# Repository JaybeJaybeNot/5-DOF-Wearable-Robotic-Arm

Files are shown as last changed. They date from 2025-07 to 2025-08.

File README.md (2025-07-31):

Robotic arms are a common project idea for engineers, providing the opportunity to tackle challenges such as feedback loops, PCB designing, firmware programming, and mechanical designing. The difficulty varies greatly, from using basic Microservos driven by Arduino to using industry-standard MCUs like the STM32 family to achieve impressive torque, precision, accuracy, and speed. 
Our design will lean somewhat to the right (industry-like) side of difficulty, utilizing the STM32F103C8Tx model of MCU's for performance, TMC motor drivers, the motors will be  2 NEMA 23 (QSH6018) for shoulders, and NEMA 17 (QSH6018) for elbow. Stepper motors are chosen for their high torque relative to their low costs, possibly getting away with $30 for each NEMA 23, depending on the seller. Gearboxes will be utilized for each motor to increase torque output. We'll also lean into the gritty, brutalist aesthetic of industry, partially because I had minimal CAD experience at the beginning of this project.
The "quirk" of our project is that the robotic arm will be wearable. Current design ideas include straps similar to those of a hiking backpack, but will possible change in the future due to ergonomic reasons or if I just came up with better ideas. To control the robotic arm, a GUI will be made with sliders that control each joint, and activators for motor modes (Stealthchop2, spreadcycle). 

This project was made out of a desire to learn embedded systems, firmware code, and basic mechanical design. It is also partially motivated by having Viktor from Arcane as my favorite character. 

Screenshot 2025-07-26 at 5 40 39 AM
Screenshot 2025-07-31 at 12 21 03 AM
Screenshot 2025-07-31 at 12 26 04 AM

|120R1 |FerriteBead |~ |Inductor_SMD:L_0402_1005Metric |1  |FIELD6|
|---|---|---|---|---|---|
|C1 |680 uF |~ |Capacitor_SMD:C_1210_3225Metric |1  | |
|C2 |220 uF |~ |Capacitor_SMD:C_0603_1608Metric |1  | |
|C3,C15 |10 pF |~ |-- mixed values -- |2  | |
|C4,C18,C19,C22,C25,C26,C27,C28|100nF |~ |-- mixed values -- |8  | |
|C5,C24 |2.2u, 6.3v |~ |-- mixed values -- |2  | |
|C6,C7,C8,C9,C14 |100 nF |~ |Capacitor_SMD:C_0201_0603Metric |5  | |
|C10 |10 uF |~ |Capacitor_SMD:C_0201_0603Metric |1  | |
|C11 |10 nF |~ |Capacitor_SMD:C_0201_0603Metric |1  | |
|C12,C13 |1 uF |~ |Capacitor_SMD:C_0201_0603Metric |2  | |
|C16,C17 |22 uF |~ |Capacitor_SMD:C_0201_0603Metric |2  | |
|C20,C29 |100uF |~ |Capacitor_SMD:CP_Elec_5x3.9 |2  | |
|C21,C23 |22nF |~ |Capacitor_SMD:C_0201_0603Metric |2  | |
|D1 |1N5824 |http://www.vishay.com/docs/88526/1n5820.pdf |Diode_THT:D_DO-201AD_P3.81mm_Vertical_AnodeUp |1  | |
|D2 |LED |~ |LED_THT:LED_D2.0mm_W4.0mm_H2.8mm_FlatTop |1  | |
|J1,J2 |Conn_01x04_Pin |~ |Connector:FanPinHeader_1x04_P2.54mm_Vertical |2  | |
|J3,J4,J5,J6,J7,J8,J9,J10 |Screw_Terminal_01x01|~ |TerminalBlock_MetzConnect:TerminalBlock_MetzConnect_360271_1x01_Horizontal_ScrewM3.0_Boxed|8  | |
|J11 |Supply anode |~ |TerminalBlock_Phoenix:TerminalBlock_Phoenix_MKDS-1,5-2-5.08_1x02_P5.08mm_Horizontal |1  | |
|J12 |Supply Cathode |~ |TerminalBlock_Phoenix:TerminalBlock_Phoenix_MKDS-1,5-2-5.08_1x02_P5.08mm_Horizontal |1  | |
|L1 |33 uH |~ |Inductor_SMD:L_0603_1608Metric |1  | |
|P1 |USB_C_Plug_USB2.0 |https://www.usb.org/sites/default/files/documents/usb_type-c.zip|Connector_USB:USB_C_Plug_JAE_DX07P024AJ1 |1  | |
|R1 |10k |~ |Resistor_SMD:R_0603_1608Metric |1  | |
|R2,R11,R12 |5.1kR |~ |Resistor_SMD:R_0603_1608Metric |3  | |
|R3,R4,R5,R6 |1.5k |~ |Resistor_SMD:R_0603_1608Metric |4  | |
|R7,R8,R9,R10 |0.05 R |~ |Resistor_SMD:R_0603_1608Metric |4  | |
|RREF1,RREF2 |0.05R |~ |Resistor_SMD:R_0603_1608Metric |2  | |
|SW1 |SW_DPST_x2 |~ |Button_Switch_SMD:SW_SPST_REED_CT05-XXXX-J1 |1  | |
|SW2 |SW_SPDT |~ |Button_Switch_THT:SW_Slide_SPDT_Straight_CK_OS102011MS2Q |1  | |
|U1 |STM32F103C8Tx |https://www.st.com/resource/en/datasheet/stm32f103c8.pdf |Package_QFP:LQFP-48_7x7mm_P0.5mm |1  | |
|U2 |AMS1117-3.3 |http://www.advanced-monolithic.com/pdf/ds1117.pdf |Package_TO_SOT_SMD:SOT-223-3_TabPin2 |1  | |
|U3,U5 |TMC2209-LA |TMC2209-LA |footprints:QFN28_5X5_TRI |2  | |
|U4 |LM2596S-3.3 |http://www.ti.com/lit/ds/symlink/lm2596.pdf |Package_TO_SOT_SMD:TO-263-5_TabPin3 |1  | |
|Y1 |16 MHz |~ |Crystal:Crystal_SMD_0603-4Pin_6.0x3.5mm |1  | |

|Part Name |FIXED Modular design|FIELD3 |FIELD4 |FIELD5|FIELD6 |FIELD7 |FIELD8 |FIELD9  |FIELD10|FIELD11 |FIELD12 |FIELD13 |
|---|---|---|---|---|---|---|---|---|---|---|---|---|
|Working BOM |as of July 31, 2025 at 12:54:05 AM UTC| | | | | | | | | | | |
|Exported by |yaoy26@okemosk12.net| | | | | | | | | | | |
|Time of Export |12:54 AM Jul 31, 2025| | | | | | | | | | | |
| | | | | | | | | | | | | |
|Level |Part Number |Part Name |External Component |Milestone|Description |Link |Lifecycle|Revision|State  |Quantity|Material Name|Change Order|
|1 |FIXED Modular design|FIXED Modular design | | | | | | |Working|1 |Steel | |
|1.1 |90304A311_Steel Pan Head Torx Screws|90304A311_Steel Pan Head Torx Screws |External | |STEP AP203 | | | |Working|1 |Steel | |
|1.2 |FLANGE_COUPLING_W_GRUB_SCREW_ASM|flange_coupling_w_grub_screw_asm |External | | |[(May not work on some browsers)](https://www.aliexpress.us/item/3256801265414698.html?gatewayAdapt=glo2usa4itemAdapt)| | |Working|1 |Steel | |
|1.2.1 |M6X8_GRUB_SCREW |M6X8_GRUB_SCREW | | |NOT SPECIFIED | | | |Working|1 |Steel | |
|1.2.2 |FLANGE_COUPLING_W_KEYWAY|FLANGE_COUPLING_W_KEYWAY | | |NOT SPECIFIED |https://www.aliexpress.us/item/2255800648228548.html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| | |Working|3 |Steel | |
|1.3 |23HS22-2804S-HG50 |23HS22-2804S-HG50 |External | |STEP AP214 |https://www.omc-stepperonline.com/nema-23-stepper-motor-l-56mm-gear-ratio-50-1-high-precision-planetary-gearbox-23hs22-2804s-hg50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| | |Working|4 |Steel | |
|1.4.1 |M6X8_GRUB_SCREW |M6X8_GRUB_SCREW (2) | | |NOT SPECIFIED | | | |Working|1 |Steel | |
| | | | | | | | | | | | | |
|1.5 |90304A311_Steel Pan Head Torx Screws|90304A311_Steel Pan Head Torx Screws v1 (1) | | |STEP AP203 | | | |Working|1 |Steel | |
|1.6 |Base2 |Base2 | | | | | | |Working|1 |Steel | |
|1.7 |Link 2 |Link 2 | | | | | | |Working|1 |Steel | |
|1.7.1 |ST-M2 |ST-M2 v1 (1) | | |STEP AP214 |https://www.omc-stepperonline.com/nema-23-bracket-for-stepper-motor-and-geared-stepper-motor-alloy-steel-bracket-st-m2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| | |Working|4 |Steel | |
|1.9 |Base1 |Base1 | | | | | | |Working|1 |Steel | |

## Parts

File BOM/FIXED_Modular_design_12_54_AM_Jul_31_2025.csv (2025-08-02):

Part Name | FIXED Modular design
Working BOM | as of July 31, 2025 at 12:54:05 AM UTC
Exported by | yaoy26@okemosk12.net
Time of Export | 12:54 AM Jul 31, 2025
Level | Part Number | Part Name | External Component | Milestone | Description | Item Number | Lifecycle | Revision | State | Quantity | Material Name | Change Order
1 | FIXED Modular design | FIXED Modular design |  |  |  |  |  |  | Working | 1 | Steel
1.1 | 90304A311_Steel Pan Head Torx Screws | 90304A311_Steel Pan Head Torx Screws | External |  | STEP AP203 |  |  |  | Working | 1 | Steel
1.2 | FLANGE_COUPLING_W_GRUB_SCREW_ASM | flange_coupling_w_grub_screw_asm | External |  |  |  |  |  | Working | 1 | Steel
1.2.1 | M6X8_GRUB_SCREW | M6X8_GRUB_SCREW |  |  | NOT SPECIFIED |  |  |  | Working | 1 | Steel
1.2.2 | FLANGE_COUPLING_W_KEYWAY | FLANGE_COUPLING_W_KEYWAY |  |  | NOT SPECIFIED |  |  |  | Working | 1 | Steel
1.3 | 23HS22-2804S-HG50 | 23HS22-2804S-HG50 | External |  | STEP AP214 |  |  |  | Working | 1 | Steel
1.4 | FLANGE_COUPLING_W_GRUB_SCREW_ASM | flange_coupling_w_grub_screw_asm v1 (2) |  |  |  |  |  |  | Working | 1 | Steel
1.4.1 | M6X8_GRUB_SCREW | M6X8_GRUB_SCREW (2) |  |  | NOT SPECIFIED |  |  |  | Working | 1 | Steel
1.4.2 | FLANGE_COUPLING_W_KEYWAY | FLANGE_COUPLING_W_KEYWAY (2) |  |  | NOT SPECIFIED |  |  |  | Working | 1 | Steel
1.5 | 90304A311_Steel Pan Head Torx Screws | 90304A311_Steel Pan Head Torx Screws v1 (1) |  |  | STEP AP203 |  |  |  | Working | 1 | Steel
1.6 | Base2 | Base2 |  |  |  |  |  |  | Working | 1 | Steel
1.7 | Link 2 | Link 2 |  |  |  |  |  |  | Working | 1 | Steel
1.7.1 | ST-M2 | ST-M2 v1 (1) |  |  | STEP AP214 |  |  |  | Working | 1 | Steel
1.8 | 23HS22-2804S-HG50 | 23HS22-2804S-HG50 v1 (2) |  |  | STEP AP214 |  |  |  | Working | 1 | Steel
1.9 | Base1 | Base1 |  |  |  |  |  |  | Working | 1 | Steel
1.10 | 23HS22-2804S-HG50 | 23HS22-2804S-HG50 v1 |  |  | STEP AP214 |  |  |  | Working | 1 | Steel
1.11 | STM32 Other motors 1 | STM32 Other motors v1 |  |  | KiCad electronic assembly |  |  |  | Working | 1 | Steel
1.11.1 | TerminalBlock_Phoenix_MKDS-1,5-2-5.08_1x02_P5.08mm_Horizontal | TerminalBlock_Phoenix_MKDS-1,5-2-5.08_1x02_P5.08mm_Horizontal |  |  |  |  |  |  | Working | 2 | Steel
1.11.1.1 | TerminalBlock_Phoenix_MKDS_15_2_508_1x02_P508mm_Horizontal | TerminalBlock_Phoenix_MKDS_15_2_508_1x02_P508mm_Horizontal |  |  |  |  |  |  | Working | 1 | Steel
1.11.2 | FanPinHeader_1x04_P2.54mm_Vertical | FanPinHeader_1x04_P2.54mm_Vertical |  |  |  |  |  |  | Working | 2 | Steel
1.11.2.1 | Fan_Pin_Header_Straight_1x04 | Fan_Pin_Header_Straight_1x04 |  |  |  |  |  |  | Working | 1 | Steel
1.11.3 | C_0201_0603Metric | C_0201_0603Metric (1) |  |  |  |  |  |  | Working | 4 | Steel
1.11.3.1 | C_0201_0603Metric | C_0201_0603Metric |  |  |  |  |  |  | Working | 1 | Steel
1.11.4 | R_0402_1005Metric | R_0402_1005Metric (1) |  |  |  |  |  |  | Working | 7 | Steel
1.11.4.1 | R_0402_1005Metric | R_0402_1005Metric |  |  |  |  |  |  | Working | 1 | Steel
1.11.5 | C_01005_0402Metric | C_01005_0402Metric (1) |  |  |  |  |  |  | Working | 18 | Steel
1.11.5.1 | C_01005_0402Metric | C_01005_0402Metric |  |  |  |  |  |  | Working | 1 | Steel
1.11.6 | R_0201_0603Metric | R_0201_0603Metric (1) |  |  |  |  |  |  | Working | 2 | Steel
1.11.6.1 | R_0201_0603Metric | R_0201_0603Metric |  |  |  |  |  |  | Working | 1 | Steel
1.11.7 | C_0402_1005Metric | C_0402_1005Metric (1) |  |  |  |  |  |  | Working | 3 | Steel
1.11.7.1 | C_0402_1005Metric | C_0402_1005Metric |  |  |  |  |  |  | Working | 1 | Steel
1.11.8 | CP_Elec_5x3.9 | CP_Elec_5x3.9 |  |  |  |  |  |  | Working | 2 | Steel
1.11.8.1 | CP_Elec_5x39 | CP_Elec_5x39 |  |  |  |  |  |  | Working | 1 | Steel
1.11.9 | C_1210_3225Metric | C_1210_3225Metric (1) |  |  |  |  |  |  | Working | 1 | Steel
1.11.9.1 | C_1210_3225Metric | C_1210_3225Metric |  |  |  |  |  |  | Working | 1 | Steel
1.11.10 | LQFP-48_7x7mm_P0.5mm | LQFP-48_7x7mm_P0.5mm |  |  |  |  |  |  | Working | 1 | Steel
1.11.10.1 | LQFP_48_7x7mm_P05mm | LQFP_48_7x7mm_P05mm |  |  |  |  |  |  | Working | 1 | Steel
1.11.11 | R_1206_3216Metric | R_1206_3216Metric (1) |  |  |  |  |  |  | Working | 4 | Steel
1.11.11.1 | R_1206_3216Metric | R_1206_3216Metric |  |  |  |  |  |  | Working | 1 | Steel
1.11.12 | TO-263-5_TabPin3 | TO-263-5_TabPin3 |  |  |  |  |  |  | Working | 1 | Steel
1.11.12.1 | CQ assembly | CQ assembly |  |  |  |  |  |  | Working | 1 | Steel
1.11.13 | R_0805_2012Metric | R_0805_2012Metric (1) |  |  |  |  |  |  | Working | 1 | Steel
1.11.13.1 | R_0805_2012Metric | R_0805_2012Metric |  |  |  |  |  |  | Working | 1 | Steel
1.11.14 | STM32 Other motors_PCB | STM32 Other motors_PCB |  |  |  |  |  |  | Working | 1 | Steel
1.11.15 | C_0603_1608Metric | C_0603_1608Metric (1) |  |  |  |  |  |  | Working | 1 | Steel
1.11.15.1 | C_0603_1608Metric | C_0603_1608Metric |  |  |  |  |  |  | Working | 1 | Steel
1.11.16 | SW_Slide_SPDT_Straight_CK_OS102011MS2Q | SW_Slide_SPDT_Straight_CK_OS102011MS2Q (1) |  |  |  |  |  |  | Working | 1 | Steel
1.11.16.1 | SW_Slide_SPDT_Straight_CK_OS102011MS2Q | SW_Slide_SPDT_Straight_CK_OS102011MS2Q |  |  |  |  |  |  | Working | 1 | Steel
1.11.17 | SW_SPST_REED_CT05-XXXX-J1 | SW_SPST_REED_CT05-XXXX-J1 |  |  |  |  |  |  | Working | 1 | Steel
1.11.17.1 | ASSEMBLY | ASSEMBLY |  |  |  |  |  |  | Working | 1 | Steel
1.11.18 | LED_D2.0mm_W4.0mm_H2.8mm_FlatTop | LED_D2.0mm_W4.0mm_H2.8mm_FlatTop (1) |  |  |  |  |  |  | Working | 1 | Steel
1.11.18.1 | LED_D2.0mm_W4.0mm_H2.8mm_FlatTop | LED_D2.0mm_W4.0mm_H2.8mm_FlatTop |  |  |  |  |  |  | Working | 1 | Steel
1.11.19 | L_0402_1005Metric | L_0402_1005Metric (1) |  |  |  |  |  |  | Working | 2 | Steel
1.11.19.1 | L_0402_1005Metric | L_0402_1005Metric |  |  |  |  |  |  | Working | 1 | Steel
1.11.20 | SOT-223 | SOT-223 |  |  |  |  |  |  | Working | 1 | Steel
1.11.20.1 | SOT_223 | SOT_223 |  |  |  |  |  |  | Working | 1 | Steel
1.11.21 | Crystal_SMD_0603-4Pin_6.0x3.5mm | Crystal_SMD_0603-4Pin_6.0x3.5mm |  |  |  |  |  |  | Working | 1 | Steel
1.11.21.1 | SMD_0603_4Pin | SMD_0603_4Pin |  |  |  |  |  |  | Working | 1 | Steel
1.12 | ST-M2 | ST-M2 v1 |  |  | STEP AP214 |  |  |  | Working | 1 | Steel
1.13 | FLANGE_COUPLING_W_GRUB_SCREW_ASM | flange_coupling_w_grub_screw_asm v1 |  |  |  |  |  |  | Working | 1 | Steel
1.13.1 | FLANGE_COUPLING_W_KEYWAY | FLANGE_COUPLING_W_KEYWAY |  |  | NOT SPECIFIED |  |  |  | Working | 1 | Steel
1.13.2 | M6X8_GRUB_SCREW | M6X8_GRUB_SCREW |  |  | NOT SPECIFIED |  |  |  | Working | 1 | Steel
1.14 | Base2 (1) | Base2 (1) |  |  |  |  |  |  | Working | 1 | Steel
1.15 | STM32 Other motors 1 | STM32 Other motors v1 (1) |  |  | KiCad electronic assembly |  |  |  | Working | 1 | Steel
1.15.1 | C_01005_0402Metric | C_01005_0402Metric (1) (1) |  |  |  |  |  |  | Working | 18 | Steel
1.15.1.1 | C_01005_0402Metric | C_01005_0402Metric (2) |  |  |  |  |  |  | Working | 1 | Steel
1.15.2 | SOT-223 | SOT-223 (1) |  |  |  |  |  |  | Working | 1 | Steel
1.15.2.1 | SOT_223 | SOT_223 (1) |  |  |  |  |  |  | Working | 1 | Steel
1.15.3 | R_1206_3216Metric | R_1206_3216Metric (1) (1) |  |  |  |  |  |  | Working | 4 | Steel
1.15.3.1 | R_1206_3216Metric | R_1206_3216Metric (2) |  |  |  |  |  |  | Working | 1 | Steel
1.15.4 | CP_Elec_5x3.9 | CP_Elec_5x3.9 (1) |  |  |  |  |  |  | Working | 2 | Steel
1.15.4.1 | CP_Elec_5x39 | CP_Elec_5x39 (1) |  |  |  |  |  |  | Working | 1 | Steel
1.15.5 | Crystal_SMD_0603-4Pin_6.0x3.5mm | Crystal_SMD_0603-4Pin_6.0x3.5mm (1) |  |  |  |  |  |  | Working | 1 | Steel
1.15.5.1 | SMD_0603_4Pin | SMD_0603_4Pin (1) |  |  |  |  |  |  | Working | 1 | Steel
1.15.6 | C_0201_0603Metric | C_0201_0603Metric (1) (1) |  |  |  |  |  |  | Working | 4 | Steel
1.15.6.1 | C_0201_0603Metric | C_0201_0603Metric (2) |  |  |  |  |  |  | Working | 1 | Steel
1.15.7 | R_0402_1005Metric | R_0402_1005Metric (1) (1) |  |  |  |  |  |  | Working | 7 | Steel
1.15.7.1 | R_0402_1005Metric | R_0402_1005Metric (2) |  |  |  |  |  |  | Working | 1 | Steel
1.15.8 | TerminalBlock_Phoenix_MKDS-1,5-2-5.08_1x02_P5.08mm_Horizontal | TerminalBlock_Phoenix_MKDS-1,5-2-5.08_1x02_P5.08mm_Horizontal (1) |  |  |  |  |  |  | Working | 2 | Steel
1.15.8.1 | TerminalBlock_Phoenix_MKDS_15_2_508_1x02_P508mm_Horizontal | TerminalBlock_Phoenix_MKDS_15_2_508_1x02_P508mm_Horizontal (1) |  |  |  |  |  |  | Working | 1 | Steel
1.15.9 | LED_D2.0mm_W4.0mm_H2.8mm_FlatTop | LED_D2.0mm_W4.0mm_H2.8mm_FlatTop (1) (1) |  |  |  |  |  |  | Working | 1 | Steel
1.15.9.1 | LED_D2.0mm_W4.0mm_H2.8mm_FlatTop | LED_D2.0mm_W4.0mm_H2.8mm_FlatTop (2) |  |  |  |  |  |  | Working | 1 | Steel
1.15.10 | TO-263-5_TabPin3 | TO-263-5_TabPin3 (1) |  |  |  |  |  |  | Working | 1 | Steel
1.15.10.1 | CQ assembly | CQ assembly (1) |  |  |  |  |  |  | Working | 1 | Steel
1.15.11 | R_0201_0603Metric | R_0201_0603Metric (1) (1) |  |  |  |  |  |  | Working | 2 | Steel
1.15.11.1 | R_0201_0603Metric | R_0201_0603Metric (2) |  |  |  |  |  |  | Working | 1 | Steel
1.15.12 | C_0402_1005Metric | C_0402_1005Metric (1) (1) |  |  |  |  |  |  | Working | 3 | Steel
1.15.12.1 | C_0402_1005Metric | C_0402_1005Metric (2) |  |  |  |  |  |  | Working | 1 | Steel
1.15.13 | FanPinHeader_1x04_P2.54mm_Vertical | FanPinHeader_1x04_P2.54mm_Vertical (1) |  |  |  |  |  |  | Working | 2 | Steel
1.15.13.1 | Fan_Pin_Header_Straight_1x04 | Fan_Pin_Header_Straight_1x04 (1) |  |  |  |  |  |  | Working | 1 | Steel
1.15.14 | R_0805_2012Metric | R_0805_2012Metric (1) (1) |  |  |  |  |  |  | Working | 1 | Steel
1.15.14.1 | R_0805_2012Metric | R_0805_2012Metric (2) |  |  |  |  |  |  | Working | 1 | Steel
1.15.15 | LQFP-48_7x7mm_P0.5mm | LQFP-48_7x7mm_P0.5mm (1) |  |  |  |  |  |  | Working | 1 | Steel
1.15.15.1 | LQFP_48_7x7mm_P05mm | LQFP_48_7x7mm_P05mm (1) |  |  |  |  |  |  | Working | 1 | Steel
1.15.16 | SW_Slide_SPDT_Straight_CK_OS102011MS2Q | SW_Slide_SPDT_Straight_CK_OS102011MS2Q (1) (1) |  |  |  |  |  |  | Working | 1 | Steel
1.15.16.1 | SW_Slide_SPDT_Straight_CK_OS102011MS2Q | SW_Slide_SPDT_Straight_CK_OS102011MS2Q (2) |  |  |  |  |  |  | Working | 1 | Steel
1.15.17 | L_0402_1005Metric | L_0402_1005Metric (1) (1) |  |  |  |  |  |  | Working | 2 | Steel
1.15.17.1 | L_0402_1005Metric | L_0402_1005Metric (2) |  |  |  |  |  |  | Working | 1 | Steel
1.15.18 | STM32 Other motors_PCB | STM32 Other motors_PCB (1) |  |  |  |  |  |  | Working | 1 | Steel
1.15.19 | C_1210_3225Metric | C_1210_3225Metric (1) (1) |  |  |  |  |  |  | Working | 1 | Steel
1.15.19.1 | C_1210_3225Metric | C_1210_3225Metric (2) |  |  |  |  |  |  | Working | 1 | Steel
1.15.20 | SW_SPST_REED_CT05-XXXX-J1 | SW_SPST_REED_CT05-XXXX-J1 (1) |  |  |  |  |  |  | Working | 1 | Steel
1.15.20.1 | ASSEMBLY | ASSEMBLY (1) |  |  |  |  |  |  | Working | 1 | Steel
1.15.21 | C_0603_1608Metric | C_0603_1608Metric (1) (1) |  |  |  |  |  |  | Working | 1 | Steel
1.15.21.1 | C_0603_1608Metric | C_0603_1608Metric (2) |  |  |  |  |  |  | Working | 1 | Steel
1.16 | ST-M2 | ST-M2 v1 (2) |  |  | STEP AP214 |  |  |  | Working | 1 | Steel
1.17 | bananaforscale | bananaforscale v1 |  |  |  |  |  |  | Working | 1 | Steel
1.18 | 23HS22-2804S-HG50 | 23HS22-2804S-HG50 v1 (1) |  |  | STEP AP214 |  |  |  | Working | 1 | Steel
1.19 | Link1 | Link1 |  |  |  |  |  |  | Working | 1 | Steel
1.20 | FLANGE_COUPLING_W_GRUB_SCREW_ASM | flange_coupling_w_grub_screw_asm v1 (1) |  |  |  |  |  |  | Working | 1 | Steel
1.20.1 | FLANGE_COUPLING_W_KEYWAY | FLANGE_COUPLING_W_KEYWAY (1) |  |  | NOT SPECIFIED |  |  |  | Working | 1 | Steel
1.20.2 | M6X8_GRUB_SCREW | M6X8_GRUB_SCREW (1) |  |  | NOT SPECIFIED |  |  |  | Working | 1 | Steel
1.21 | 90304A311_Steel Pan Head Torx Screws | 90304A311_Steel Pan Head Torx Screws v1 |  |  | STEP AP203 |  |  |  | Working | 1 | Steel

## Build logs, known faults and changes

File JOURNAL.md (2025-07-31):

---
Title: "Wearable 5 axis Robotic Arm"
author: "Yugang Yao"
description: "Fully custom stepper motor robotic arm you can wear on your back, operating like a fully controllable third arm by interacting with a GUI."
created at: 2025-7-4
TOTAL HOURS: 50 Hr 15 Minutes (Not including time spent planning, debugging, or reading datasheets because I didn't record them)
---

$${\color{white}06/15/2025 \space project \space statement \space and \space planning}$$

I have an idea!

Problem statement: Two arms can get everything done. But a third one can be nifty, huh? Even if it’s for simple applications, it can still be vastly useful. What if you’re holding everything in your two arms, and you need to open a door? What if you are typing and want to get a glass of water to your lips without breaking momentum? What if, possibly, you are performing a surgery and need some assistance? What if you’re doing some sort of combat sport, and want to get a bit creative? What if you just wanna show off at parties?

Objectives: wearable Robotic arm that follows the following specifications:  

5 degrees of freedom: wrist, elbow, shoulder roll, shoulder pitch, gripper. 

Graphical User interface that controls arm movements.

minimum payload 100-300 g

Angular accuracy: +/- 2-3 degrees with high-resolution servos or steppers+encoders

Position repeatability: 1-2 mm at full reach. Depends on backlash and compliance

Backlash: <0.5mm. Use zero backlash gearboxes or direct drive.

Delay must be <=500 ms from user input to motor response.

 Should stay relatively still when “attached” to the user’s back
 
Should have a safety mechanism so the user doesn’t get shocked by the 24v battery

I may use the local college’s lab to get some cheap hardware. I doubt they have the exact parts, but they may potentially have potentiometers, resistors, capacitors, Microcontrollers, etc. 

PLANNING:

VNH5019 modules for motor driving have already been designed and are available for $15-20 a pop. You see, we’re kinda budget-tight, so we’re going to design a PCB with 4 of the bare VNH5019A-E ICs–$5 each– to attach to our Maxon EC-i 40 + GP 10 A gearbox. Also note that the VNH5019 only drives brushed motors.

$${\color{white}5/16/2025}$$

Stepper motor possibility (but a few hours later)

The brushed DC motor mentioned earlier is gonna set us back 120 dollars each. We can use a NEMA 23 stepper motor with a large gearbox ratio for the desired torque output instead. Currently thinking 20:1, but I’ll have to see a more experienced engineer later to see if that is possible. Because stepper motors kinda can’t be run using the VNH5019, we’ll instead look into the possibilities of the TMC2226 motor driver. 

Update: We’re going with the NEMA 23 stepper motor with TMC 2226 motor driver

Possibilities of using in revision:
1. harmonic/planatery reducer for motors to extract highest torque instead
2. Using encoders (AS5600, AS5048A) instead of potentiometer for position feedback. Can be a bit more expensive, and we’ll have to learn some things. 

$${\color{white}6/18/2025}$$

Break: Heart project
All that planning for the Robotic arm project is stressing me out. So we’re gonna take a break and make a PCB with LED lights in the shape of a heart, lighting up in sequence. This is the schematics I made. 
Utilizes 2 IC’s:  555 timer to send clock signals in astable mode, and DC4017 to “chase” LEDs in a sequence. Powered by 3 coin batteries, of course. 
Screenshot 2025-07-01 at 11 36 05 AM

I’ll either add this to the robotic arm, or give it as a trinket to my friend. They gave me a heart keychain a few months ago. Regardless, I’ll make the PCB layout for this in my next break. 

I can also possibly modify the design to make it act as an error tester later on the road. 

**1 hour**

$${\color{white}6/22/2026}$$

We’re on vacation, so progress is slow. A wrist-mounted control panel for the arm would be cool as hell, no? We’ll probably have to take on even more disciplines though… Like Embedded UI, power management, and probably ergonomics. Bluetooth for communication, maybe a charge controller for safety, a TFT LCD for affordability and durability, and a MCU for the spi communication; Perhaps an ESP 32 would suit the application. I’ll add this as an idea for next iterations of the arm.

The design for the PCB with the TMC2226-SA motor driver has been commenced, and will probably finish by the end of the day. Moving on next, we’ll figure out the programming and software, and where we can get the mechanical design for the arm. We’ll also tinker around with ROS2, and use Gazebo for simulation (let’s also copy paste the URDF files for the actual arm). My old computer has Ubuntu installed, so let’s do that. 

We can potentially use the 24V battery volt source to power the Nano by using a LM2596 voltage regulator.

Today’s progress (Elbow joint driver and MCU):
Screenshot 2025-06-27 at 9 21 26 PM

**3 hours**

$${\color{white}7/1/2025}$$

Just came back after climbing Mount HuangShan, it was peak (ahahaha).

Anyways, gonna crank out the basic PID code for the arduino nano and for driving the NEMA 17. Honestly, I am quite inexperienced on implementing PID, even though I know alot about the theory. 

I work in bursts anyways, so hopefully I can get most of it done today.
Today’s code:

Screenshot 2025-07-04 at 8 53 39 AM
**3.5 hours**

$${\color{white}7/2/2025}$$

Further project planning + parts selecting

Ok, so, we’re gonna keep the pcb Designs, but there will no longer be any centralized PCB (like as if it’s a critical hit area in a video game). Essentially, the drivers will be placed right next to the motors in the form of small PCB’s, with terminals connecting from the base, which houses the MCU, voltage regulator, and whatnot. Wait, so the 24v power supply to the motors will have a long wire too? I wonder if that’ll introduce even more problems.

To offset this, we’ll make the power supply slightly larger than 24V to compensate for the higher resistance (26v, 28v). We’ll also add a bulk cap (100-470 uF) decoupling capacitor as well as a ceramic cap (0.1-1uF).  right next to Vin of Drivers, as well as ferret beads on the power supply line right before the driver. This is a pretty crude, unelegant method but it’ll probably be enough.

Main reason we’re still using our own design for the motor drivers is because they’re lowk expensive ($30+) and too big to fit in the joints.

Final decision:

Main PCB will sit at base of robotic arm, containing the STM32 Bluepill (STM32F103C8Tx); 2 motor drivers for shoulder yaw and shoulder pitch; and a voltage regulator connected to 24v power source. Elbow joint will have their own motor driver for the TMC2209 NEMA 17

Tmc 2209-LA info:
Footprints and symbol
Datasheet
Finally decided on the specific models:
Nema 17
Nema23
(There are links to these in the original doc)

Reminder, Driver compatibility is about matching current, voltage, and inductance to the driver’s chopping frequency and thermal rating!
Thus, the TCM2226-SA will be used to drive the NEMA 17, while the dual TCM2209-LA will be used to drive the NEMA 23. 
Today's schematic progress (so far):
Screenshot 2025-07-04 at 8 57 01 AM

Iteration for Mark II:
Just watched 稚晖君’s video on his dummy robotic arm, and felt kinda envious when compared to my own design. Thus, I have a wishlist for Mark II in case I build a second robotic arm:
CAN bus
Per-joint MCUs
Force sensors
(Encoders instead of potentiometers)
Sleeker driver IC layouts
Smarter GUI
Power optimization
AI vision 
(optional) glove to control robotic arm movement

For now, we just need to worry about making A robotic arm. 

Taking notes on TMC2209 driver features:

Stealthchop: Silent operation, good for lower velocities

Significantly improved microstepping with low-cost motors - Motor runs smooth and quiet - Absolutely no standby noise - Reduced mechanical resonance yields improved torque

Spreadcycle: Good for higher velocities.

After a few hours, I have finished the schematic FULLY, and have reviewed it to have no errors (so far, I will review it once more when I prepare for PCB layout). Here is the full schematic:Screenshot 2025-07-04 at 2 53 10 PM

I should probably add redundancies for overheating, since running all these on the same PCB will fry it easily. But I feel like moving on to software for now, so that’ll have to wait until I prepare for the PCB layout.

Btw ignore PB5. I've already removed that label; it's just a small error.

**8 hours total**

$${\color{white}7/6/2025}$$

Ok, platformIO is acting up.
Not only did I lose the Main.cpp file for the main PCB board, but I literally can’t find the folder itself. The folder is also nowhere to be seen on the project tab of VScode. 

So, we’re gonna ditch platformIO for STM32CubeIDE.

Hip hip hooray! We get to rewrite the ENTIRE code for the main PCB, but this time in HAL =D! I can’t WAIT to basically learn a whole different language =DDDDDDDD. 

Just played around with STM32cubeIDE for a while, and learned from guides/documentations on youtube. Phil’s Lab my GOAT fr

Screenshot 2025-07-06 at 4 02 45 AM

Ran into some problems with the clock configurations, seems like the APB1 peripheral clock frequency is too low. 

Screenshot 2025-07-06 at 4 02 58 AM

After some tweaking and painfully reading the STM32F1 reference manual, this minor speedbump has been remedied. 

Screenshot 2025-07-06 at 4 03 08 AM

Pins are configured, and so are the clocks. Now all we have to do is figure out how to set the STM32 up to receive serial from the Mac, what to do with certain info, and create the GUI. Finally, we’ll create the 3D physical model and we’ll be done. 

**3 hours**

Note: Kinda been dodging a core problem right now, but we gotta confront the fact that carrying around a 24v battery can kinda cause some lowkey agonizing pain if something goes wrong. So we'll have to overload on safety mechanisms when we get to mechanical design. We'll also have to make additions on our PCB to further prevent overheating

$${\color{white}7/17/2025}$$

Just came back from camp, back to the grind. This also means we’ll have to ramp up productivity. A review of the arm:
Shoulder 
1. will have 3 D.O.F.
2. 2 NEMA motors will be driven by main PCB,
3. 3rd one will be driven by Arduino Nano interfaced via I2C 
STM32F1 will be master MCU. We have 48 MHz of processing power and we will use the full 48 MHz of it!
4.Power source: 24 volts, will be placed in a heavily insulated box to prevent shocks
Elbow:
A singular Arduino nano and TMC driver for Nema 17. 
Further iterations might utilize belts to lower torque on elbow
Wrist: Simple MG90 servo. Just use PWM vro 
GUI: will be built in tkinter. Interfaces with the Uart serial to STM32. 
Alright, today we’ll get serial done, and begin on the mechanical design.

This means we'll gonna have to LEARN UART programming, including HAL and serial parsing. Here's the code so far: Screenshot 2025-07-18 at 9 26 53 PM

**5 Hours**

$${\color{white}7/23/2025-7/25/2025}$$

I have chipped down the DRC more and more on clearance violations, and have connected the pins together finally. We have decided to use GND and power planes for noise and emi reduction, though it will be a bit more expensive. 

We have also finally added PCBway constraints into the settings. Thus, we’ll have to switch from 0402 components to larger ones, because lowk they’re unable to tolerate the close proximity of the components. 

Screenshot 2025-07-26 at 5 03 54 AM

Screenshot 2025-07-26 at 5 04 09 AM

We WILL add heat pours in the future—after finishing the DRC.

I have also met with a longtime friend, a Umich alumni in robotics about this design. he says it’s good so far, so that’s something to think about =].

**12 hours**

May seem like a long time, but trust me, I haven’t done something this complex before so I MUST make sure everything runs as good as possible. 

$${\color{white}7/26/2025}$$

Yayyyy, mechanical design! Woohoo, Yippee.

Constraints:

1. 0.5-1 meters

2. 2 kg payload minimum.

3. Fully covering circuitry

4. Openable via screws to access circuitry and wires

5. Separate compartment for wires and circuitry

6. Hexagonal comb design. Will have one side honeycomb, the other three sides will be solid

7. 25:1 gearboxes, compromise for torque and speed

8. 7075 or 6061 aluminum for linkages. More Carbon fiber towards end of arm. Steel for joints and base.

9. Planetary gearboxes for zero backlash if we can afford it (probably not for the first design. May be employed for future iterations )

10. Modular end factor for different attachable functions. Module will have plugs that attach to end factor to communicate to a microcontroller on what to do. Will also have latches to maintain connection.

Alright, let's get started.

The specs are as follows: shoulder (base) will have 3 degrees of freedom to mimic actual human arm. Will contain the main PCB, alongside slave MCU PCB to drive the additional motor. The motors will all be NEMA 23s.

The elbow joint will be 1 D.O.F. and uses arduino nano + TMC2226SA for the Nema 17. Will also interface with main PCB. Only comment lightly on the fact that we're using I2C protocol for the ~.33m distance between the main mcu and slave mcu.

The wrist will use SG90S microservo. Optional, actually.

Link length from** shoulder joints to elbow joint will be .33 m**. From** elbow to wrist is .46 m.**

All 3 shoulder motors will be placed closely together at the base to reduce torque

**Joints decisions:**

1. Shoulders:

1. Options:

1. Welded Pivot Bracket joint.

1. Pros:

1. extremely strong and rigid,

2. zero backlash.

2. Cons:

3. Permanent. Make a mistake? Womp womp, you can’t fix it.  You also can’t take them out, so they’re not modular

4. You kinda need to know how to weld, and get welding equipment (DEALBREAKER)

2. **Bolt on bracket system (WE’RE USING THIS ONE)**

3. Pros:

5. Still pretty strong

6. Bolted, not welded (NOT DEALBREAKER)

7. Looks pretty clean

2. Elbow:

2. Clevis + Pin Joint.

3. Pro:

4. Can be laser cutted

5. Pretty compact

6. Strong enough

7. VEX robotics people use it

4. Con:

8. Need retainer clips or shoulder bolts

9. **Needs TIGHT tolerances**

Let’s not talk about end effector for now.

Of course, we’ll also need:

1. Bearings

1. 10 mm bore, 26mm OD Flanged bearing

2. Shaft link hub / coupler

3. Shaft collar

4. Mounting brackets or housing to hold bearings in place and constrain all movements except rotation

2. One side must hold rigidity, (bearing pocket or press-fit)

5. Spacer(s) and Shoulder Bolt / Axle Bolt

3. Prevents axial shrifting, keeps rotations smooth

4. Space prevents the bearing from rubbing against joint arm or frame. Shoulder bolt has a section that fits bearing ID perfectly.

We’ll mount the Nema 17 at elbow. But if we NEED to optimize torque, then we can just place them at the back with a belt loop.

rectangular holes are probably for ventilation and weight \; we’ll employ that.

**1 Hour**

**7/27/2025**

Mechanical design marathon.

Aluminum 6061 is very expensive, [datasheet](https://asm.matweb.com/search/specificmaterial.asp?bassnum=ma6061t6) . So here’s the plan:

1. At the base, we’ll use some sort of steel alloy. Cheaper, but 3 times the density

2. Aluminum 5052 could be a substitute.

I feel the plan right now is model a rough diagram of the arm on paper, create a multidimensional function of stress, strain, load, and torque in terms of density of the material selected, and the width/girth of the arm. THEN we'll choose the components based on our application.

Alright, we’ve finished the analysis of the arm at it’s worst scenario: Perfectly horizontal.

Screenshot 2025-07-30 at 5 43 59 PM

**30 minutes**

Not gonna do other angles, because we’ve already accounted for worst case scenario. Also, it’s probably not likely that it’ll just collapse on itself if i raise it perfectly vertical even if the axial stress is at its strongest.

Time for parts selection!

Code for calculations:

import math

==== Inputs ====
Geometry (in meters)
L1 = 0.33      # Length of Link 1

L2 = 0.46      # Length of Link 2

w = 0.1     # Width of rectangular cross-section

h = 0.1       # Height (thickness) of rectangular cross-section

Material (Aluminum 6061-T6)
E = 68.9e9             # Modulus of Elasticity (Pa)

sigma_y = 276e6        # Yield Strength (Pa)

tau_y = 207e6          # Shear Strength (Pa)

fatigue_strength = 96.5e6 # Fatigue Strength (Pa)

Density = 2700 #kg/m^3

Masses (kg)
m1 = L1 * Density * w * h       # Mass of Link 1

m2 = L2 * Density * w * h       # Mass of Link 2

payload = 4200                 # force from punch or weight (Newtons)

Angle of payload force relative to the link axis (in degrees)
theta_deg = 0

theta = math.radians(theta_deg)

Safety Factor
FoS = 1.5

Gravity
g = 9.81  # m/s^2

==== Derived geometric properties ====
A = w * h                         # Cross-sectional area

I = (w * h**3) / 12               # Second moment of area

c = h / 2                         # Distance from neutral axis

==== Forces ====
P_parallel = payload * math.cos(theta) # Axial component

P_perp = payload * math.sin(theta)     # Transverse (bending) component

==== Torques ====
tau_elbow = m2 * g * (L2 / 2) + P_perp * L2

tau_shoulder = (m1 * g * (L1 / 2) +m2 * g * (L1 + L2 / 2) +P_perp * (L1 + L2))

==== Stresses ====
sigma_axial = P_parallel / A

sigma_bending = ((P_perp * (L1 + L2) + (m1 * g * L1/2) + (m2*g*(L1 + L2/2)))  * c) / I

sigma_total = sigma_axial + sigma_bending

AFoS = 276e6 / sigma_total

==== Strain ====
strain = sigma_total / E

==== Deflection ====
Tip deflection of link 2 under end load only
delta = (P_perp * L2**3) / (3 * E * I)

==== Checks ====
print("=== ROBOTIC ARM STRESS REPORT ===")

print(f"Axial Stress:      {sigma_axial/1e6:.2f} MPa")

print(f"Bending Stress:    {sigma_bending/1e6:.2f} MPa")

print(f"Total Stress:      {sigma_total/1e6:.2f} MPa")

print(f"Strain:            {strain:.5e}")

print(f"Deflection (L2):   {delta*1000:.2f} mm")

print(f"Elbow Torque:      {tau_elbow:.2f} Nm")

print(f"Shoulder Torque:   {tau_shoulder:.2f} Nm")

print(f"factor of safety:   {AFoS}")

print("\n=== SAFETY CHECK ===")

print(f"Yield Limit ({sigma_y/FoS/1e6:.2f} MPa) : {'Yessir!' if sigma_total < sigma_y / FoS else 'No =['}")

print(f"Fatigue Limit ({fatigue_strength/FoS/1e6:.2f} MPa): {'Yessir!' if sigma_total < fatigue_strength / FoS else 'No =['}")

print(f"Deflection Check (< {L2/250:.2e} m): {'Yessir!' if delta < L2/250 else 'No =['}")

We’ll play around with the variables until we find something desirable.

****15 minutes****

Ok so, it turns out that if we were to go with a 0.1 m x 0.1 m approximate cross sectional area of the arm using aluminum 6061, we’ll need 28 Nm of torque… Nema 17 can only produce 0.14-0.75 nm max. We’ll have to redo the PCB to change the Nema 17 to a Nema 23. On top of that, aluminum 6061 is frick-ton expensive even if hollow(~$200 for one link), so we’ll have to find other materials and compromise.

Material alternatives:

1. [Steel 1018](https://www.mwcomponents.com/uploads/Resource-Center/Elgin-Material-Sheets/Carbon-Steel-Grade-1018-Data-Sheet_Elgin.pdf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)

1. 370 MPa yield

2. [A36 steel](https://www.ryerson.com/metal-resources/metal-market-intelligence/a36-steel-plate)

2. 248.2 MPa yield

Material selection later. Let’s just design the arm now.

We’ll begin with the joint, constraint definitions: \
1. Houses Nema 23 motor

2. Houses the gearbox along the Nema 23 motor

3. Rotate well

4. Holes for wires to connect with motor

There will be 2 type of joints; the shoulder joint, and elbow joint.

That’s basically it honestly

We originally considered HTD5 timing pulleys, but that’s too mechanically advanced for me. So we’re going to use **NEMA23 ****<span style="text - decoration: underline;">worm**</span>** gearbox (50:1)** as simple add ons to the motor. Cheaper than planetory, and we don’t need industrial level precision so we may get away with $150 total. 

[Nema 23 sizes](http://www.piclist.com/techref/io/stepper/nemasizes.htm)

*Just learned the method is called a **Euler angle joint** chain mimicking the **glenohumeral (shoulder) joint**

The first base will be larger than the second base to compensate for having to carry extra weight. We might have to “overengineer: the coupling between the bases to prevent backlash and slippage. Of course the final rotational joint will just be bolt on bracket.

Enter image alt description
[example image](https://www.researchgate.net/figure/The-iCub-arm-A-CAD-view-of-the-arm-of-the-iCub-robot-with-superimposed-joint-labels-th_fig3_229010855)

Enter image alt description
[inexpensive planetory gearboxes](https://www.omc-stepperonline.com/nema-23-stepper-motor-l-56mm-gear-ratio-50-1-high-precision-planetary-gearbox-23hs22-2804s-hg50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) 

<span style="text - decoration: underline;">**7/29/2025**</span>

(TORQUE POTENTIALLY TOO LOW)

Ugh, it seems we’ll have to go searching for gearboxes again.

We’ll use **Aliexpress** if we need to. 

Screenshot 2025-07-30 at 5 45 40 PM

We’ll add bearings to this sliding point later to both reduce stress on the main motor and to reduce friction. Oh, and the lid for this part will be honeycomb pattern for aesthetics and saving on material.

I’m back with the design, and I just realized.

LOOK AT THE SIZE OF THAT THING HOLY C- BANANA FOR SCALE BY THE WAY.

Screenshot 2025-07-30 at 5 45 59 PM

Realistically, we have 2 options:

1. Redesign the shoulder from scratch

2. Severely cut down on the container size for each motors.

If we go with number 2, which is the most alluring option by far, we might just have the motors exposed. Cuts back on cost and torque too, I guess.

Main issue comes from the motor + gearbox, which is 0.15 m by itself. Holy-

[Direct motor mount](https://www.omc-stepperonline.com/nema-23-bracket-for-stepper-motor-and-geared-stepper-motor-alloy-steel-bracket-st-m2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), we’ll be using this 

Screenshot 2025-07-30 at 5 46 28 PM

Alright, much more manageable now. (Banana for scale)

**5 hours**

7/29/2025

Continued with the mechanical design. We had to dig through various sources to get semi fluent. In short, we’ve decided to use **bracket mounts** to hold the motors in place and **flanged couplers** to get it attached to stuff, ball bearings and honeycomb pattern pending. Of course, there are holes for the I2C wires to go through. 

Finally, we’re finished.

Screenshot 2025-07-30 at 5 46 51 PM

Now all we have to do is provide the wiring diagram, and BOM.
Screenshot 2025-07-30 at 4 51 13 PM
Screenshot 2025-07-30 at 4 46 00 PM
Screenshot 2025-07-30 at 4 37 42 PM
Screenshot 2025-07-30 at 4 36 12 PM
Screenshot 2025-07-30 at 4 31 14 PM

This is the wiring for now. Of course, **We will add clips during assembly to hold the wires down. **

*****8 hours***** (I didn’t know much about mechanical design)

Even if there are many flaws in the design; Ngl, this has been a wild month, and a wild ride. I’ll never forget the 15 hour PCB marathon on the plane. Oh, and I hope my journals entertained somebody.

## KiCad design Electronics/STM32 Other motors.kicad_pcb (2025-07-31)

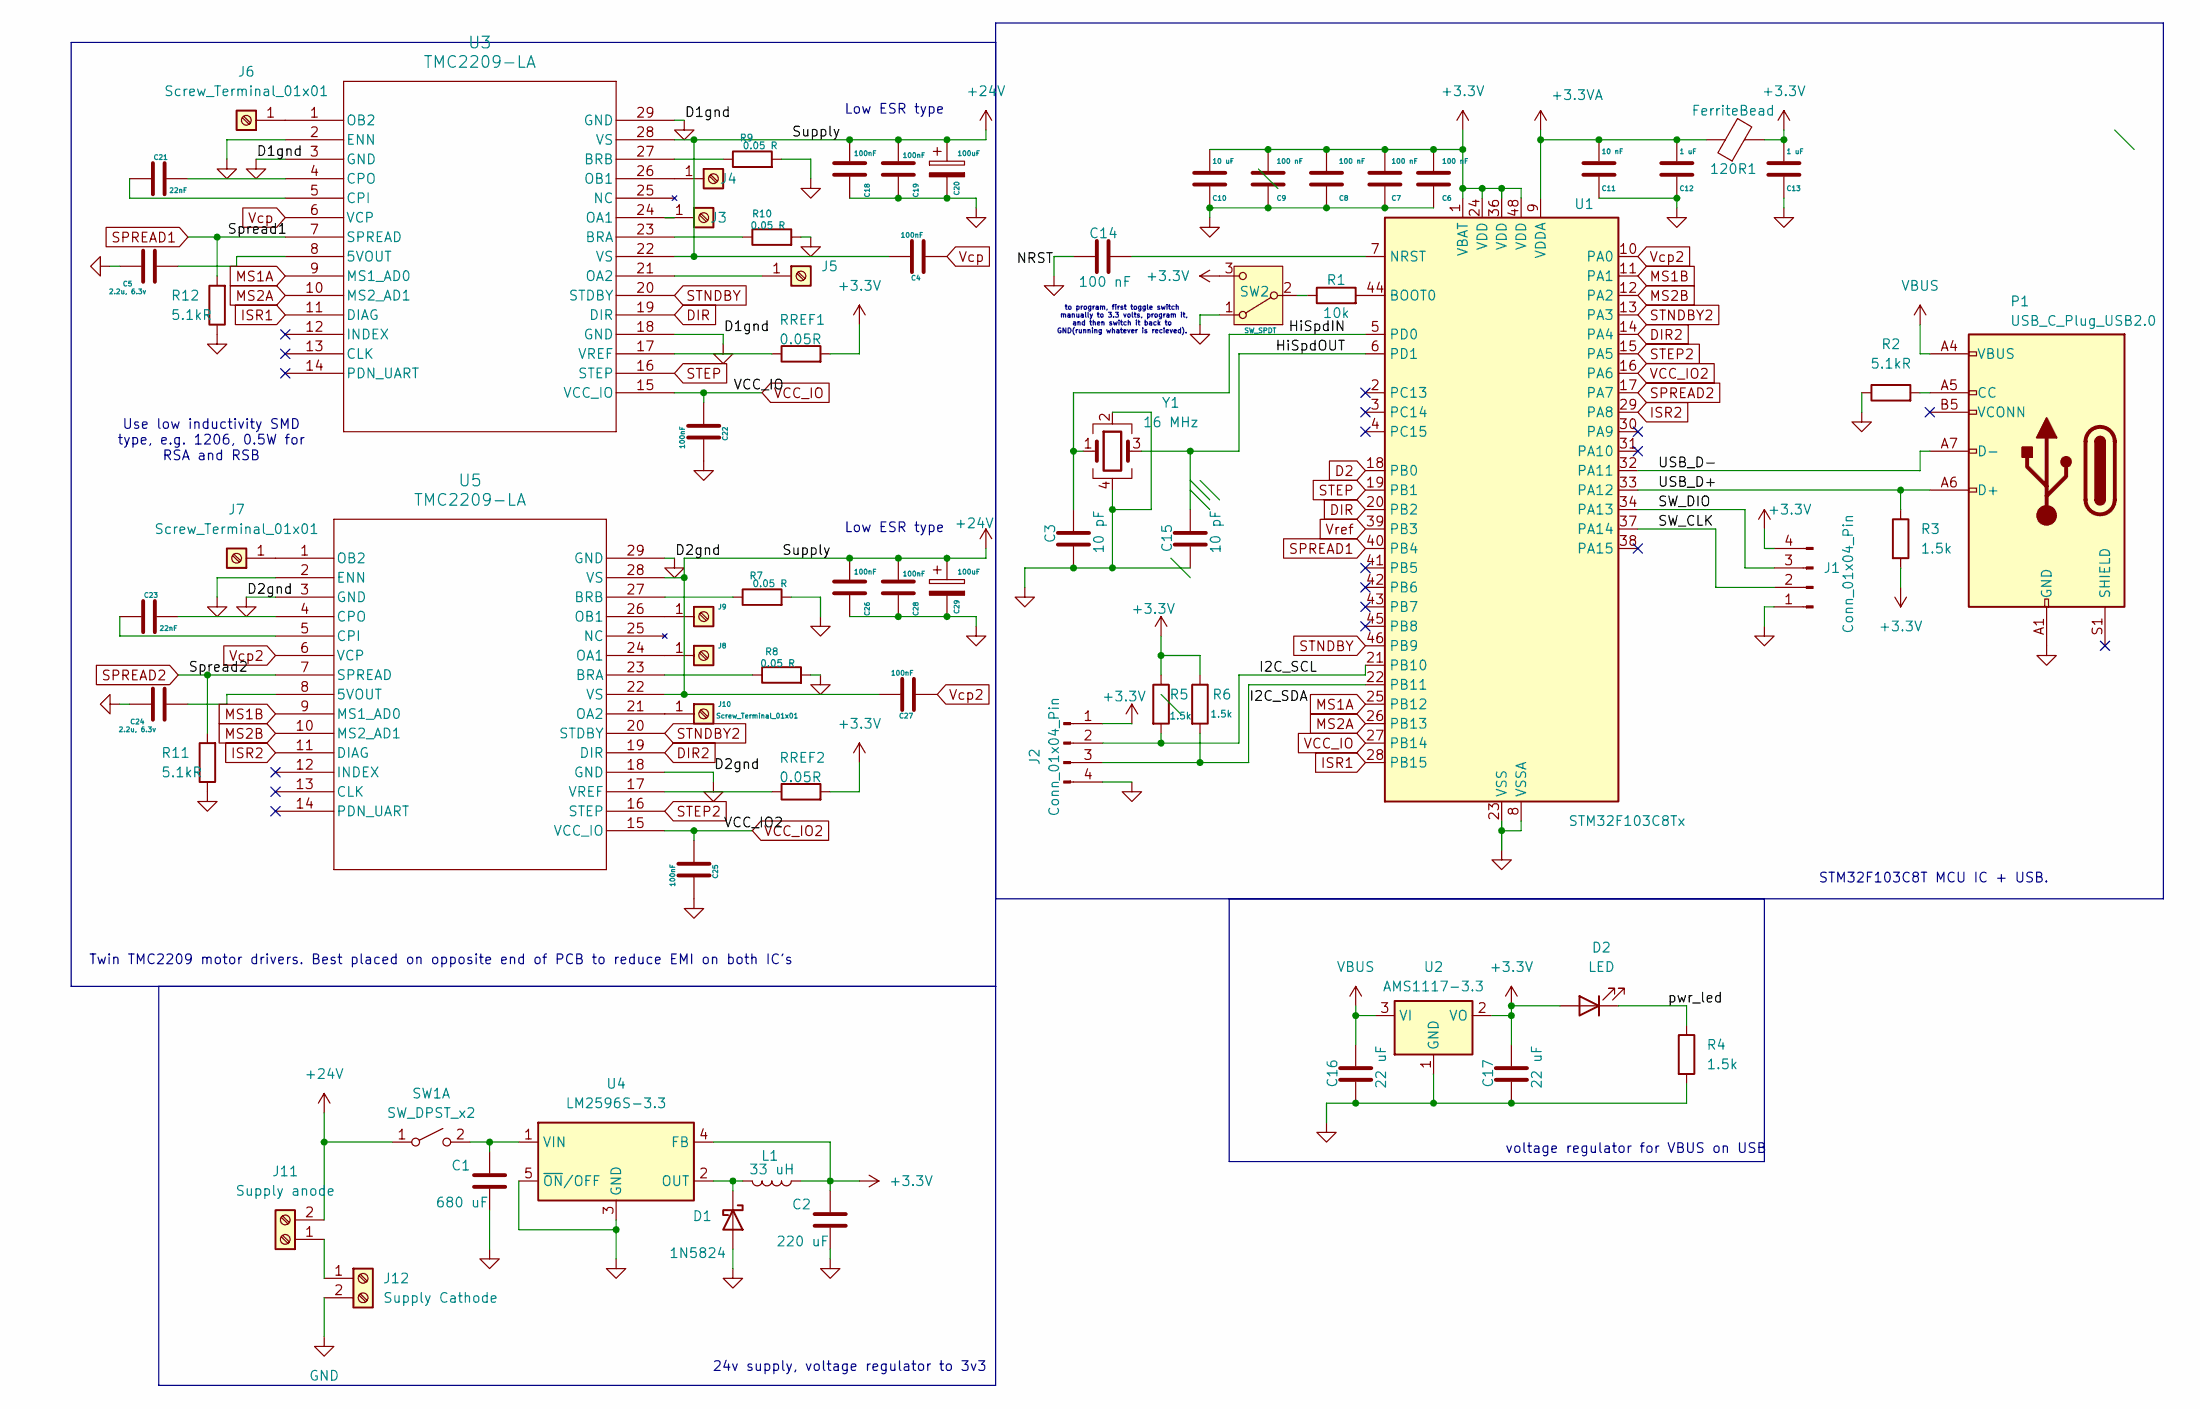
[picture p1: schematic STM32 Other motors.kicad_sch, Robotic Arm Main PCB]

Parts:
120R1: FerriteBead; L_0402_1005Metric
C1: 680 uF; C_1210_3225Metric
C2: 220 uF; C_0603_1608Metric
C3: 10 pF; C_0402_1005Metric
C4: 100nF; C_0402_1005Metric
C5: 2.2u, 6.3v; C_0402_1005Metric
C6, C7, C8, C9, C14: 100 nF; C_0201_0603Metric
C10: 10 uF; C_0201_0603Metric
C11: 10 nF; C_0201_0603Metric
C12, C13: 1 uF; C_0201_0603Metric
C15: 10 pF; C_0201_0603Metric
C16, C17: 22 uF; C_0201_0603Metric
C18, C19, C22, C25, C26, C27, C28: 100nF; C_0201_0603Metric
C20, C29: 100uF; CP_Elec_5x3.9
C21, C23: 22nF; C_0201_0603Metric
C24: 2.2u, 6.3v; C_0201_0603Metric
D1: 1N5824; D_DO-201AD_P3.81mm_Vertical_AnodeUp
D2: LED; LED_D2.0mm_W4.0mm_H2.8mm_FlatTop
J1, J2: Conn_01x04_Pin; FanPinHeader_1x04_P2.54mm_Vertical
J3, J4, J5, J6, J7, J8, J9, J10: Screw_Terminal_01x01; TerminalBlock_MetzConnect_360271_1x01_Horizontal_ScrewM3.0_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
J11: Supply anode; TerminalBlock_Phoenix_MKDS-1,5-2-5.08_1x02_P5.08mm_Horizont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
J12: Supply Cathode; TerminalBlock_Phoenix_MKDS-1,5-2-5.08_1x02_P5.08mm_Horizont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
L1: 33 uH; L_0603_1608Metric
P1: USB_C_Plug_USB2.0; USB_C_Plug_JAE_DX07P024AJ1
R1: 10k; R_0603_1608Metric
R2, R11, R12: 5.1kR; R_0603_1608Metric
R3, R4, R5, R6: 1.5k; R_0603_1608Metric
R7, R8, R9, R10: 0.05 R; R_0603_1608Metric
RREF1, RREF2: 0.05R; R_0603_1608Metric
SW1: SW_DPST_x2; SW_SPST_REED_CT05-XXXX-J1
SW2: SW_SPDT; SW_Slide_SPDT_Straight_CK_OS102011MS2Q
U1: STM32F103C8Tx; LQFP-48_7x7mm_P0.5mm
U2: AMS1117-3.3; SOT-223-3_TabPin2
U3, U5: TMC2209-LA; QFN28_5X5_TRI
U4: LM2596S-3.3; TO-263-5_TabPin3
Y1: 16 MHz; Crystal_SMD_0603-4Pin_6.0x3.5mm

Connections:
+3.3V: 120R1.2, C2.2, C6.2, C7.2, C8.2, C9.2, C10.2, C13.2, C17.1, D2.2 (A), J1.4, J2.1, L1.1, R3.2, R5.1, R6.1, RREF1.2, RREF2.2, SW2.3 (C), U1.1 (VBAT), U1.24 (VDD), U1.36 (VDD), U1.48 (VDD), U2.2 (VO), U4.4 (FB)
+3.3VA: 120R1.1, C11.2, C12.2, U1.9 (VDDA)
+24V: C4.2, C18.2, C19.2, C20.1, C26.2, C27.2, C28.2, C29.1, J11.2, SW1.1 (A), U3.22 (VS), U3.28 (VS), U5.22 (VS), U5.28 (VS)
/HiSpdIN: C3.1, U1.5 (PD0), Y1.1
/HiSpdOUT: C15.1, U1.6 (PD1), Y1.3
/I2C_SCL: J2.2, R5.2, U1.21 (PB10)
/I2C_SDA: J2.3, R6.2, U1.22 (PB11)
/SW_CLK: J1.2, U1.37 (PA14)
/SW_DIO: J1.3, U1.34 (PA13)
/USB_D+: P1.A6 (D+), R3.1, U1.33 (PA12)
/USB_D-: P1.A7 (D-), U1.32 (PA11)
/pwr_led: D2.1 (K), R4.1
D2: U1.18 (PB0)
DIR: U1.20 (PB2), U3.19 (DIR)
DIR2: U1.14 (PA4), U5.19 (DIR)
GND: C1.1, C2.1, C3.2, C5.1, C6.1, C7.1, C8.1, C9.1, C10.1, C11.1, C12.1, C13.1, C14.2, C15.2, C16.2, C17.2, C18.1, C19.1, C20.2, C22.2, C24.1, C25.2, C26.1, C28.1, C29.2, D1.2 (A), J1.1, J2.4, J12.2, P1.A1 (GND), P1.A12 (GND), P1.B1 (GND), P1.B12 (GND), R2.1, R4.2, R7.2, R8.2, R9.2, R10.2, R11.1, R12.1, SW2.1 (A), U1.8 (VSSA), U1.23 (VSS), U1.35 (VSS), U1.47 (VSS), U2.1 (GND), U3.2 (ENN), U3.3 (GND), U3.18 (GND), U3.29 (GND), U4.3 (GND), U4.5 (~ON/OFF), U5.2 (ENN), U5.3 (GND), U5.18 (GND), U5.29 (GND), Y1.2, Y1.4
ISR1: U1.28 (PB15), U3.11 (DIAG)
ISR2: U1.29 (PA8), U5.11 (DIAG)
MS1A: U1.25 (PB12), U3.9 (MS1_AD0)
MS1B: U1.11 (PA1), U5.9 (MS1_AD0)
MS2A: U1.26 (PB13), U3.10 (MS2_AD1)
MS2B: U1.12 (PA2), U5.10 (MS2_AD1)
unnamed: D1.1 (K), L1.2, U4.2 (OUT)
unnamed: J3.1, U3.24 (OA1)
unnamed: J4.1, U3.26 (OB1)
unnamed: J5.1, U3.21 (OA2)
unnamed: J6.1, U3.1 (OB2)
unnamed: J7.1, U5.1 (OB2)
unnamed: J8.1, U5.24 (OA1)
unnamed: J9.1, U5.26 (OB1)
unnamed: J10.1, U5.21 (OA2)
unnamed: J11.1, J12.1
unnamed: P1.A5 (CC), R2.2
unnamed: C1.2, SW1.2 (B), U4.1 (VIN)
unnamed: R1.1, SW2.2 (B)
unnamed: R1.2, U1.44 (BOOT0)
unnamed: C14.1, U1.7 (NRST)
unnamed: C5.2, U3.8 (5VOUT)
unnamed: R10.1, U3.23 (BRA)
unnamed: R9.1, U3.27 (BRB)
unnamed: C21.1, U3.5 (CPI)
unnamed: C21.2, U3.4 (CPO)
unnamed: RREF1.1, U3.17 (VREF)
unnamed: C24.2, U5.8 (5VOUT)
unnamed: R8.1, U5.23 (BRA)
unnamed: R7.1, U5.27 (BRB)
unnamed: C23.1, U5.5 (CPI)
unnamed: C23.2, U5.4 (CPO)
unnamed: RREF2.1, U5.17 (VREF)
SPREAD1: R12.2, U1.40 (PB4), U3.7 (SPREAD)
SPREAD2: R11.2, U1.17 (PA7), U5.7 (SPREAD)
STEP: U1.19 (PB1), U3.16 (STEP)
STEP2: U1.15 (PA5), U5.16 (STEP)
STNDBY: U1.46 (PB9), U3.20 (STDBY)
STNDBY2: U1.13 (PA3), U5.20 (STDBY)
VBUS: C16.1, P1.A4 (VBUS), P1.A9 (VBUS), P1.B4 (VBUS), P1.B9 (VBUS), U2.3 (VI)
VCC_IO: C22.1, U1.27 (PB14), U3.15 (VCC_IO)
VCC_IO2: C25.1, U1.16 (PA6), U5.15 (VCC_IO)
Vcp: C4.1, U3.6 (VCP)
Vcp2: C27.1, U1.10 (PA0), U5.6 (VCP)
Vref: U1.39 (PB3)

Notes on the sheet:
Twin TMC2209 motor drivers. Best placed on opposite end of PCB to reduce EMI on both IC's
24v supply, voltage regulator to 3v3
to program, first toggle switch manually to 3.3 volts, program it, and then switch it back to GND(running whatever is recieved).
Low ESR type
STM32F103C8T MCU IC + USB.
Use low inductivity SMD type, e.g. 1206, 0.5W for RSA and RSB
voltage regulator for VBUS on USB

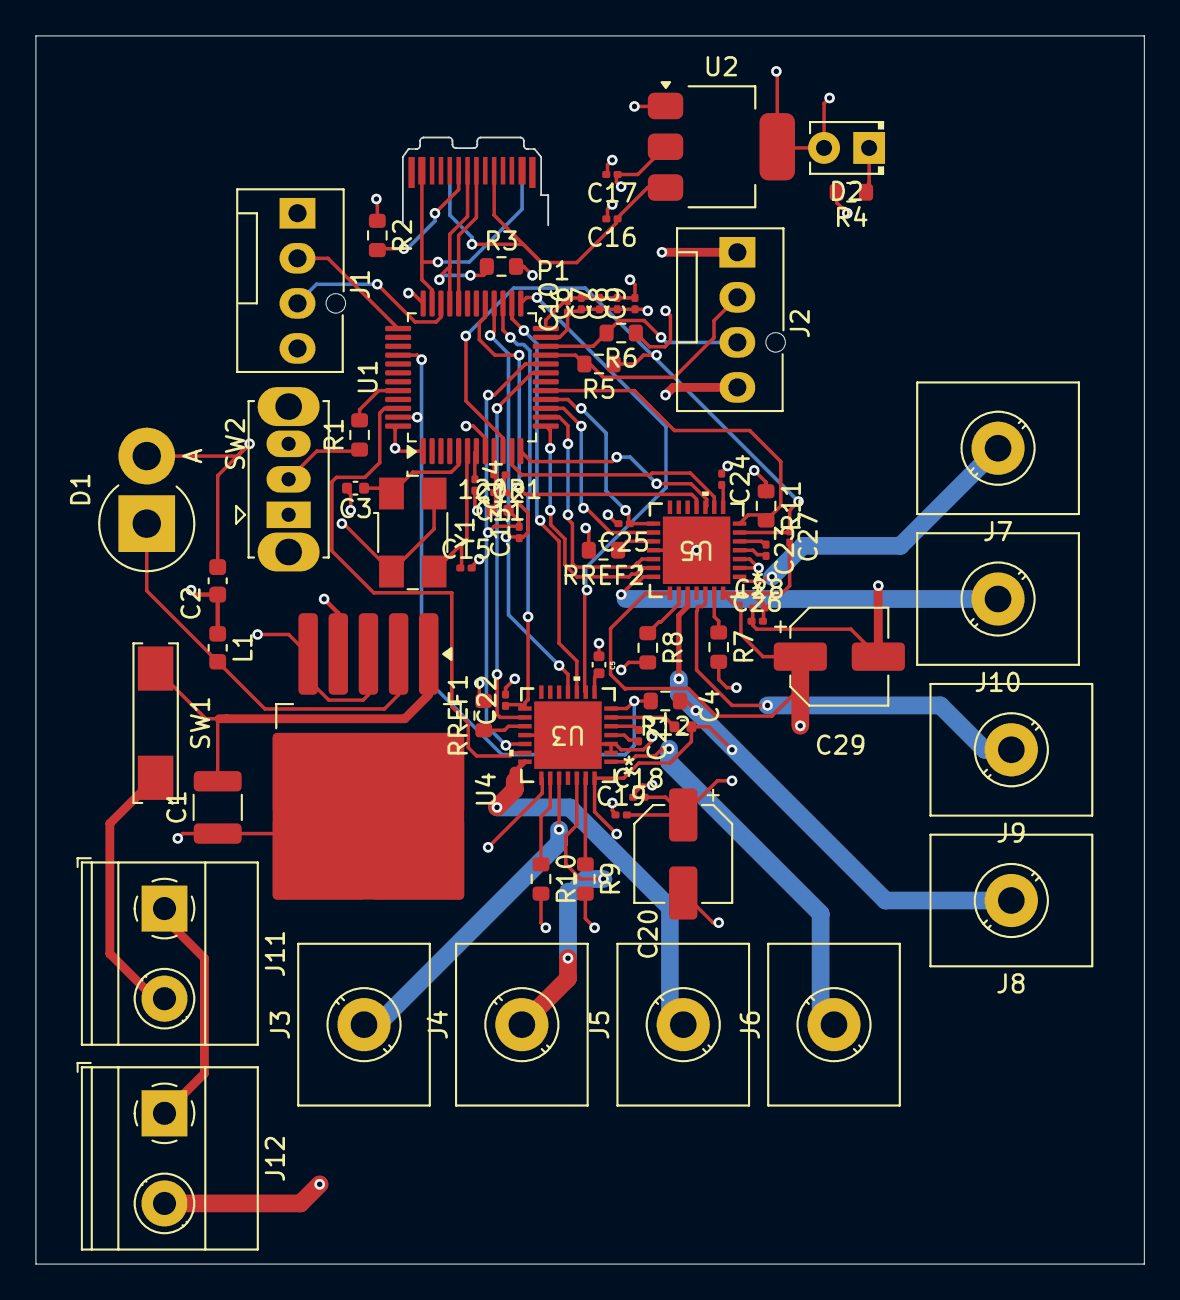
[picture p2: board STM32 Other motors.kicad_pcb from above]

Board: 4 copper layers, 62.5 x 69.2 mm, 68 parts (0 on the bottom side), 59 nets.

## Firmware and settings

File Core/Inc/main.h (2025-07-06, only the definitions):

#define Vcp2_Pin GPIO_PIN_0
#define Vcp2_GPIO_Port GPIOA
#define MS1B_Pin GPIO_PIN_1
#define MS1B_GPIO_Port GPIOA
#define MS2B_Pin GPIO_PIN_2
#define MS2B_GPIO_Port GPIOA
#define STNDBY2_Pin GPIO_PIN_3
#define STNDBY2_GPIO_Port GPIOA
#define DIR2_Pin GPIO_PIN_4
#define DIR2_GPIO_Port GPIOA
#define STEP2_Pin GPIO_PIN_5
#define STEP2_GPIO_Port GPIOA
#define VCC_IO2_Pin GPIO_PIN_6
#define VCC_IO2_GPIO_Port GPIOA
#define SPREAD2_Pin GPIO_PIN_7
#define SPREAD2_GPIO_Port GPIOA
#define D2_Pin GPIO_PIN_0
#define D2_GPIO_Port GPIOB
#define STEP_Pin GPIO_PIN_1
#define STEP_GPIO_Port GPIOB
#define DIR_Pin GPIO_PIN_2
#define DIR_GPIO_Port GPIOB
#define MS1A_Pin GPIO_PIN_12
#define MS1A_GPIO_Port GPIOB
#define MS2A_Pin GPIO_PIN_13
#define MS2A_GPIO_Port GPIOB
#define VCC_IO_Pin GPIO_PIN_14
#define VCC_IO_GPIO_Port GPIOB
#define ISR1_Pin GPIO_PIN_15
#define ISR1_GPIO_Port GPIOB
#define ISR2_Pin GPIO_PIN_8
#define ISR2_GPIO_Port GPIOA
#define USB_D__Pin GPIO_PIN_11
#define USB_D__GPIO_Port GPIOA
#define USB_D_A12_Pin GPIO_PIN_12
#define USB_D_A12_GPIO_Port GPIOA
#define Vref_Pin GPIO_PIN_3
#define Vref_GPIO_Port GPIOB
#define SPREAD1_Pin GPIO_PIN_4
#define SPREAD1_GPIO_Port GPIOB
#define STNDBY_Pin GPIO_PIN_9
#define STNDBY_GPIO_Port GPIOB

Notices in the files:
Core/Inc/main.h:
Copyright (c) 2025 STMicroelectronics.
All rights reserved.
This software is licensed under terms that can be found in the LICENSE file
